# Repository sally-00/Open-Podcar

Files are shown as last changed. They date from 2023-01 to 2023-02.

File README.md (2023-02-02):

# Open Podcar 2.0

This is a project extended from [OpenPodcar](https://github.com/OpenPodcar/OpenPodcar).

We have changed components and improved the PCB layout to allow more flexibility in the system and ensure safty while operating the car.

At current stage, we have tested the linear actuator, almost finished the design of PCB except a few further improvements.
We will mount the linear actuator, manufactor the PCB and mount all the components in the close future.

## Linear Actuator Demostration
A demostration of controlling the linear actuator with the joystick which pass the steer command to the ESP32 through ROS using Wi-Fi is shown as follows.

<a href="https://youtu.be/pCknVWg_ioM
" target="_blank">Linear Actuator Joystick Control Demostration</a>

<a href="https://youtu.be/71_QIT539q4
" target="_blank">Linear Actuator Steering Demostration</a>

## PCB design
The final schematic of the PCB is shown as follows.

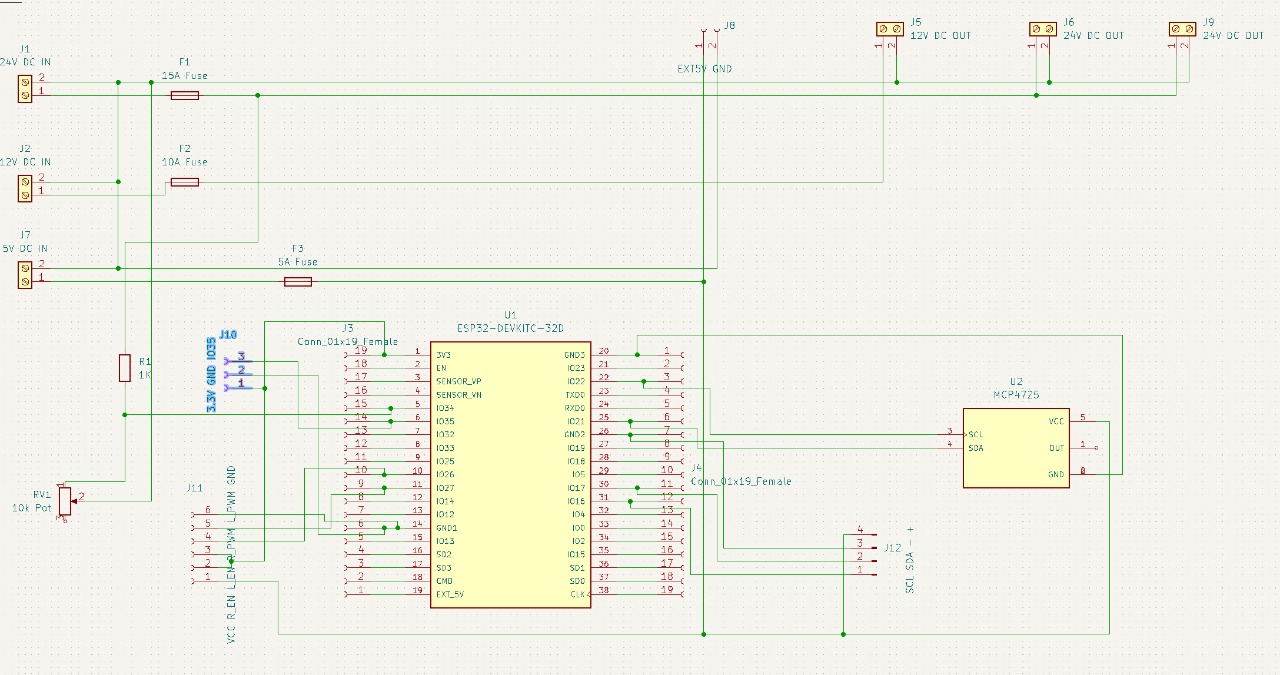
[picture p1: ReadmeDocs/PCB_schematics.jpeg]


The layout of the PCB at the current stage is shown as follows.

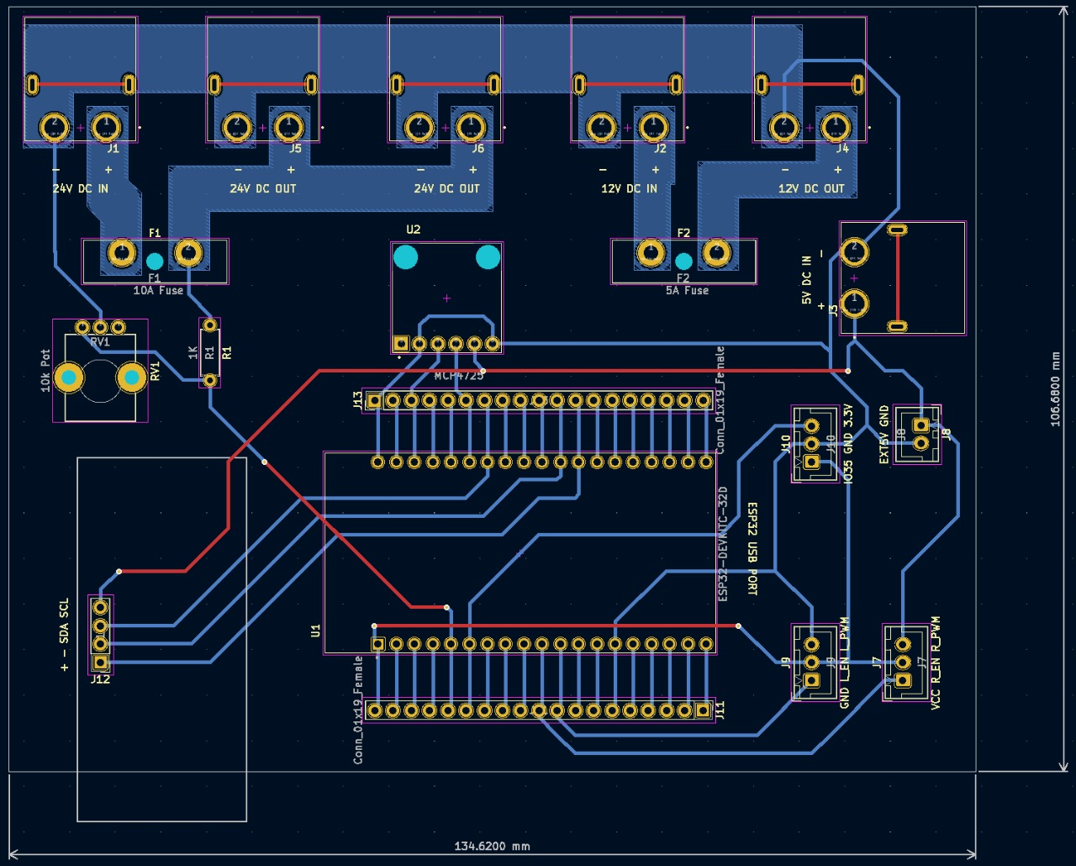
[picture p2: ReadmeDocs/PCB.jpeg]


## Bill of Materials

#### Vehicle
1 Gimson Robotics GLA750-P 12V DC linear actuator with position feedback (100mm stroke)

Metal bracket [linik to product](https://www.amazon.co.uk/dp/B08JV76967?ref_=cm_sw_r_apin_dp_HXTQEXMHK0DS5XG23BHY)

#### PCB

1 ESP32 [link to product](https://www.amazon.co.uk/XTVTX-Development-Wireless-Bluetooth-Frequency/dp/B09LCDJY8Z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)

1 DollaTek BTS7960 5.5V to 27V 43A High Power Motor Driver [link to product](https://www.amazon.co.uk/gp/product/B09H6MKWCJ/ref=ppx_yo_dt_b_asin_title_o00_s00?ie=UTF8&psc=1)

1 Digital to Analog Converter [link to product](https://www.digikey.co.uk/en/products/detail/sparkfun-electronics/BOB-12918/5140812?utm\_adgroup=Evaluation%20Boards%20-%20Digital%20to%20Analog%20Converters%20%28DACs%29&utm\_source=google&utm\_medium=cpc&utm\_campaign=Shopping\_Product\_Development%20Boards%2C%20Kits%2C%20Programmers&utm\_term=&productid=5140812&gclid=CjwKCAiAs8acBhA1EiwAgRFdw7jZpmNLCZSMikVMd7oKKiSc0wkz7JpF8sl4ogsQpp6ZFNUjAHO2KBoC\_PIQAvD_BwE)

1 Buck Converter Module 24V to 12V 15A [link to product](https://www.amazon.co.uk/dp/B01KQWWSLA/)

1 Buck Converter Module 12V to 5V 5A [link to product](https://www.amazon.co.uk/dp/B09NVZ6Y6J?ref_=cm\_sw\_r\_apin\_dp_F5CDBP8B0AESHGP8G7D0)

JST-XH connector [link to product](https://www.amazon.co.uk/YIXISI-460Pcs-Housing-Connector-Adapter/dp/B082ZLYRRN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)

Male XT60PW Gold Plated connector [link to product](https://www.switchelectronics.co.uk/male-xt60pw-gold-plated-connector-30a-amass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)

XT-60H connector [link to product](https://amzn.eu/d/4VwUmz3)

Fuse holder [link to product](https://uk.farnell.com/littelfuse/178-7017-0001/fuse-holder-pcb-r-a-blade/dp/310530?st=Ato%20fuse%20holder)

5A Fuse

10A Fuse

Potentiometer [link to product](https://uk.rs-online.com/web/p/potentiometers/8274990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)

Jumper wire [link to product](https://www.amazon.co.uk/VIPMOON-1-17mm-Multicolored-Flexible-Rainbow/dp/B07BLRNTXW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)

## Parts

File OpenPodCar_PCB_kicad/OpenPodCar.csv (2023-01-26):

Source: | C:\Users\skyks\Documents\KiCad\Projects\OpenPodCar - 2022\OpenPodCar\OpenPodCar.kicad_sch
Date: | 13/12/2022 15:54:15
Tool: | Eeschema (6.0.9)
Generator: | E:\Kicad\6.0\bin\scripting\plugins/bom_csv_grouped_by_value_with_fp.py
Component Count: | 18
Ref | Qnty | Value | Cmp name | Footprint | Description | Vendor
F1, | 1 | 15A Fuse | Fuse | Fuse:Fuseholder_Blade_ATO_Littelfuse_Pudenz_2_Pin | Fuse
F2, | 1 | 10A Fuse | Fuse | Fuse:Fuseholder_Blade_ATO_Littelfuse_Pudenz_2_Pin | Fuse
F3, | 1 | 5A Fuse | Fuse | Fuse:Fuseholder_Blade_ATO_Littelfuse_Pudenz_2_Pin | Fuse
J1, | 1 | 24V DC IN | Screw_Terminal_01x02 | TerminalBlock_MetzConnect:TerminalBlock_MetzConnect_Type011_RT05502HBWC_1x02_P5.00mm_Horizontal | Generic screw terminal, single row, 01x02, script generated (kicad-library-utils/schlib/autogen/connector/)
J2, | 1 | 12V DC IN | Screw_Terminal_01x02 |  | Generic screw terminal, single row, 01x02, script generated (kicad-library-utils/schlib/autogen/connector/)
J3, J4, | 2 | Conn_01x19_Female | Conn_01x19_Female | Connector_PinHeader_2.54mm:PinHeader_1x19_P2.54mm_Vertical | Generic connector, single row, 01x19, script generated (kicad-library-utils/schlib/autogen/connector/)
J5, | 1 | 12V DC OUT | Screw_Terminal_01x02 | TerminalBlock_MetzConnect:TerminalBlock_MetzConnect_Type011_RT05502HBWC_1x02_P5.00mm_Horizontal | Generic screw terminal, single row, 01x02, script generated (kicad-library-utils/schlib/autogen/connector/)
J6, J9, | 2 | 24V DC OUT | Screw_Terminal_01x02 | TerminalBlock_MetzConnect:TerminalBlock_MetzConnect_Type011_RT05502HBWC_1x02_P5.00mm_Horizontal | Generic screw terminal, single row, 01x02, script generated (kicad-library-utils/schlib/autogen/connector/)
J7, | 1 | 5V DC IN | Screw_Terminal_01x02 | TerminalBlock_MetzConnect:TerminalBlock_MetzConnect_Type011_RT05502HBWC_1x02_P5.00mm_Horizontal | Generic screw terminal, single row, 01x02, script generated (kicad-library-utils/schlib/autogen/connector/)
J8, | 1 | EXT5V GND | Conn_01x02_Female | Connector_PinHeader_2.54mm:PinHeader_1x02_P2.54mm_Vertical | Generic connector, single row, 01x02, script generated (kicad-library-utils/schlib/autogen/connector/)
J10, | 1 | 3.3V GND IO35 | Conn_01x03_Female | Connector_PinHeader_2.54mm:PinHeader_1x03_P2.54mm_Vertical | Generic connector, single row, 01x03, script generated (kicad-library-utils/schlib/autogen/connector/)
J11, | 1 | VCC R_EN L_EN R_PWM L_PWM | Conn_01x05_Female | Connector_PinHeader_2.54mm:PinHeader_1x05_P2.54mm_Vertical | Generic connector, single row, 01x05, script generated (kicad-library-utils/schlib/autogen/connector/)
R1, | 1 | 1K | R |  | Resistor
RV1, | 1 | 10k Pot | R_Potentiometer | Potentiometer_THT:Potentiometer_Bourns_PTV09A-1_Single_Vertical | Potentiometer
U1, | 1 | ESP32-DEVKITC-32D | ESP32-DEVKITC-32D | MODULE_ESP32-DEVKITC-32D
U2, | 1 | MCP4725 | ZC576300 | MODULE_ZC576300

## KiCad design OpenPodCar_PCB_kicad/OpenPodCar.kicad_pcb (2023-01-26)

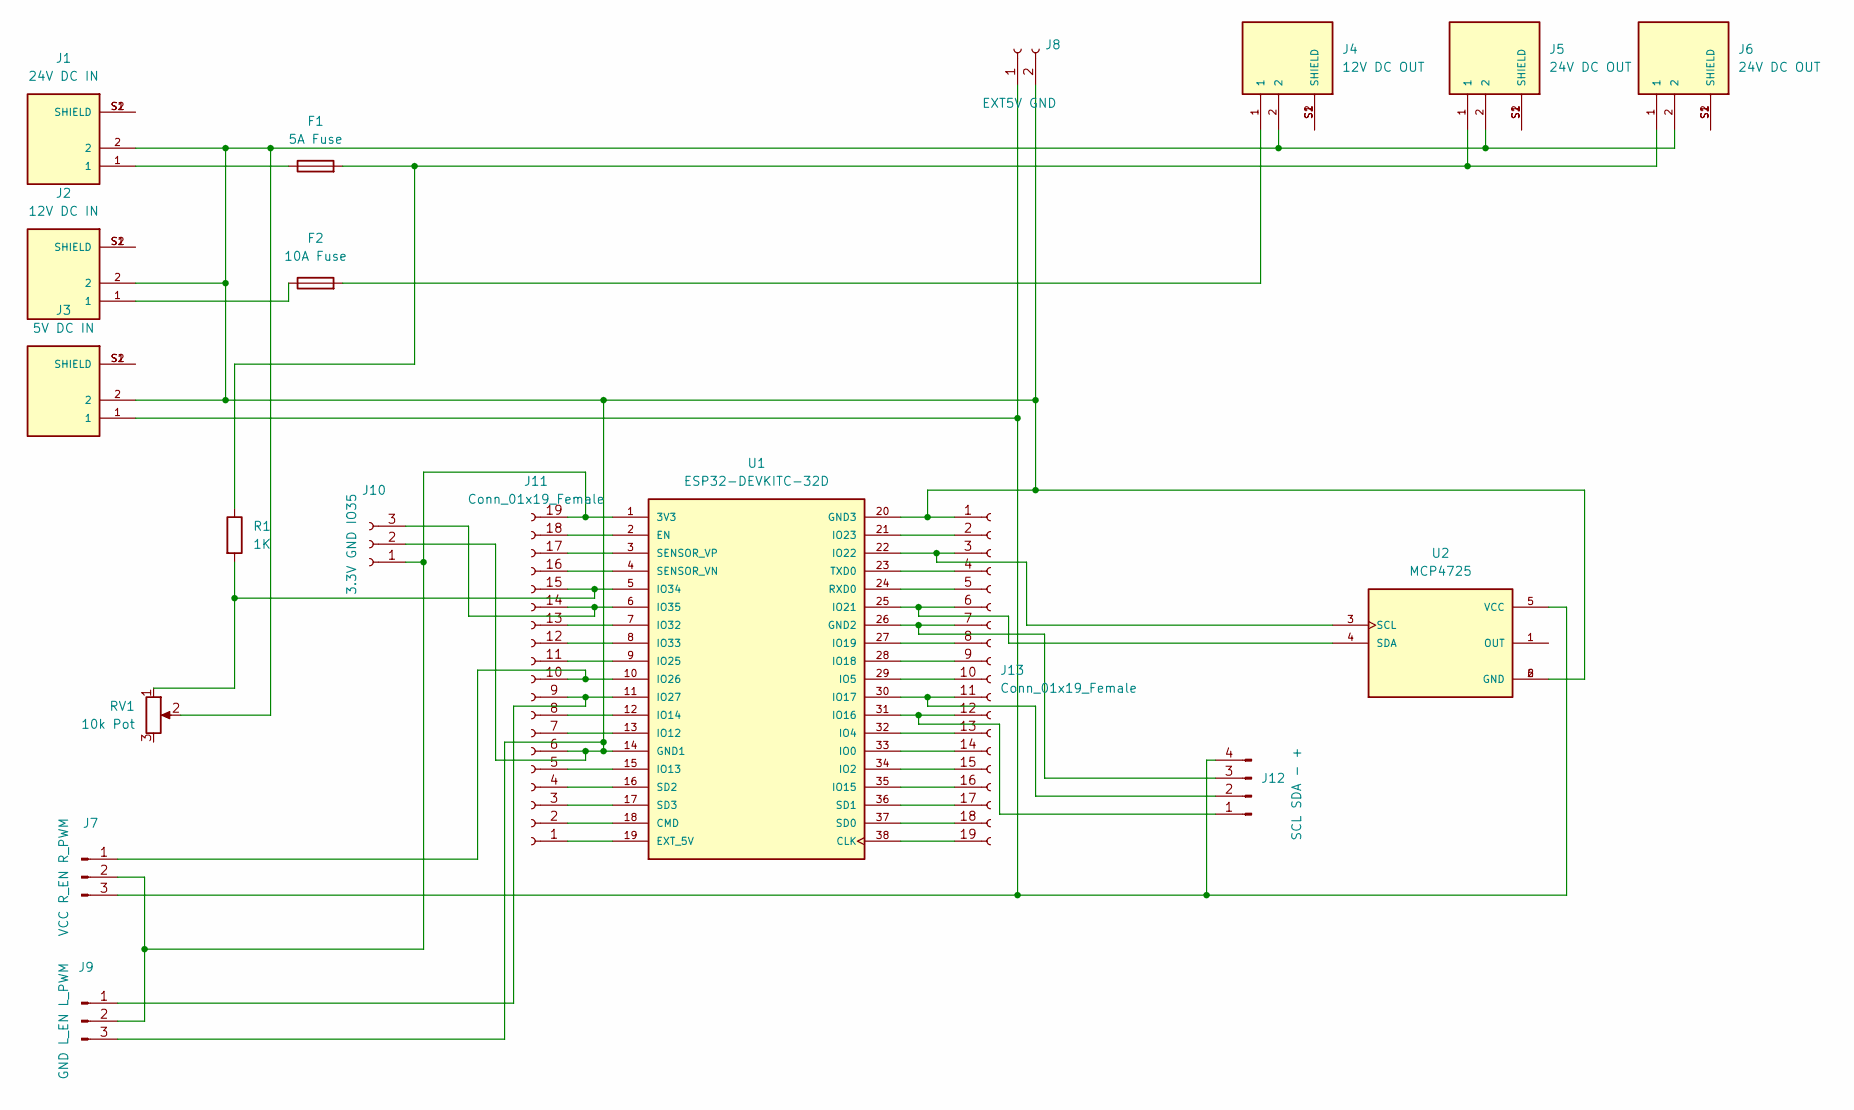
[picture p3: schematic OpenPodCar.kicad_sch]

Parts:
F1: 5A Fuse; Fuseholder_Blade_ATO_Littelfuse_Pudenz_2_Pin
F2: 10A Fuse; Fuseholder_Blade_ATO_Littelfuse_Pudenz_2_Pin
J1: 24V DC IN; AMASS_XT60PW-F; PARTREV V1.2
J2: 12V DC IN; AMASS_XT60PW-F; PARTREV V1.2
J3: 5V DC IN; AMASS_XT60PW-F; PARTREV V1.2
J4: 12V DC OUT; AMASS_XT60PW-F; PARTREV V1.2
J5, J6: 24V DC OUT; AMASS_XT60PW-F; PARTREV V1.2
J7: VCC R_EN R_PWM; JST_XH_B3B-XH-A_1x03_P2.50mm_Vertical
J8: EXT5V GND; JST_XH_B2B-XH-A_1x02_P2.50mm_Vertical
J9: GND L_EN L_PWM; JST_XH_B3B-XH-A_1x03_P2.50mm_Vertical
J10: 3.3V GND IO35; JST_XH_B3B-XH-A_1x03_P2.50mm_Vertical
J11, J13: Conn_01x19_Female; PinHeader_1x19_P2.54mm_Vertical
J12: SCL SDA - +; PinHeader_1x04_P2.54mm_Vertical
R1: 1K; R_Axial_DIN0207_L6.3mm_D2.5mm_P7.62mm_Horizontal
RV1: 10k Pot; Potentiometer_Bourns_PTV09A-1_Single_Vertical
U1: ESP32-DEVKITC-32D; MODULE_ESP32-DEVKITC-32D; PARTREV 4
U2: MCP4725; MODULE_ZC576300; PARTREV v14

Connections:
unnamed: F1.1, J1.1
unnamed: F1.2, J5.1, J6.1, R1.1
unnamed: F2.1, J2.1
unnamed: F2.2, J4.1
unnamed: J1.2, J2.2, J3.2, J4.2, J5.2, J6.2, J8.2, J9.3, J10.2, J11.6, J13.1, RV1.2, U1.14 (GND1), U1.20 (GND3), U2.2 (GND), U2.6 (GND)
unnamed: J1.S1 (SHIELD), J1.S2 (SHIELD)
unnamed: J2.S1 (SHIELD), J2.S2 (SHIELD)
unnamed: J3.S1 (SHIELD), J3.S2 (SHIELD)
unnamed: J4.S1 (SHIELD), J4.S2 (SHIELD)
unnamed: J5.S1 (SHIELD), J5.S2 (SHIELD)
unnamed: J6.S1 (SHIELD), J6.S2 (SHIELD)
unnamed: J7.2, J9.2, J10.1, J11.19, U1.1 (3V3)
unnamed: J10.3, J11.14, U1.6 (IO35)
unnamed: J11.1, U1.19 (EXT_5V)
unnamed: J11.2, U1.18 (CMD)
unnamed: J11.3, U1.17 (SD3)
unnamed: J11.4, U1.16 (SD2)
unnamed: J11.5, U1.15 (IO13)
unnamed: J11.7, U1.13 (IO12)
unnamed: J11.8, U1.12 (IO14)
unnamed: J9.1, J11.9, U1.11 (IO27)
unnamed: J7.1, J11.10, U1.10 (IO26)
unnamed: J11.11, U1.9 (IO25)
unnamed: J11.12, U1.8 (IO33)
unnamed: J11.13, U1.7 (IO32)
unnamed: J11.15, R1.2, RV1.1, U1.5 (IO34)
unnamed: J11.16, U1.4 (SENSOR_VN)
unnamed: J11.17, U1.3 (SENSOR_VP)
unnamed: J11.18, U1.2 (EN)
unnamed: J12.1, J13.12, U1.31 (IO16)
unnamed: J12.2, J13.11, U1.30 (IO17)
unnamed: J12.3, J13.7, U1.26 (GND2)
unnamed: J3.1, J7.3, J8.1, J12.4, U2.5 (VCC)
unnamed: J13.2, U1.21 (IO23)
unnamed: J13.3, U1.22 (IO22), U2.3 (SCL)
unnamed: J13.4, U1.23 (TXD0)
unnamed: J13.5, U1.24 (RXD0)
unnamed: J13.6, U1.25 (IO21), U2.4 (SDA)
unnamed: J13.8, U1.27 (IO19)
unnamed: J13.9, U1.28 (IO18)
unnamed: J13.10, U1.29 (IO5)
unnamed: J13.13, U1.32 (IO4)
unnamed: J13.14, U1.33 (IO0)
unnamed: J13.15, U1.34 (IO2)
unnamed: J13.16, U1.35 (IO15)
unnamed: J13.17, U1.36 (SD1)
unnamed: J13.18, U1.37 (SD0)
unnamed: J13.19, U1.38 (CLK)

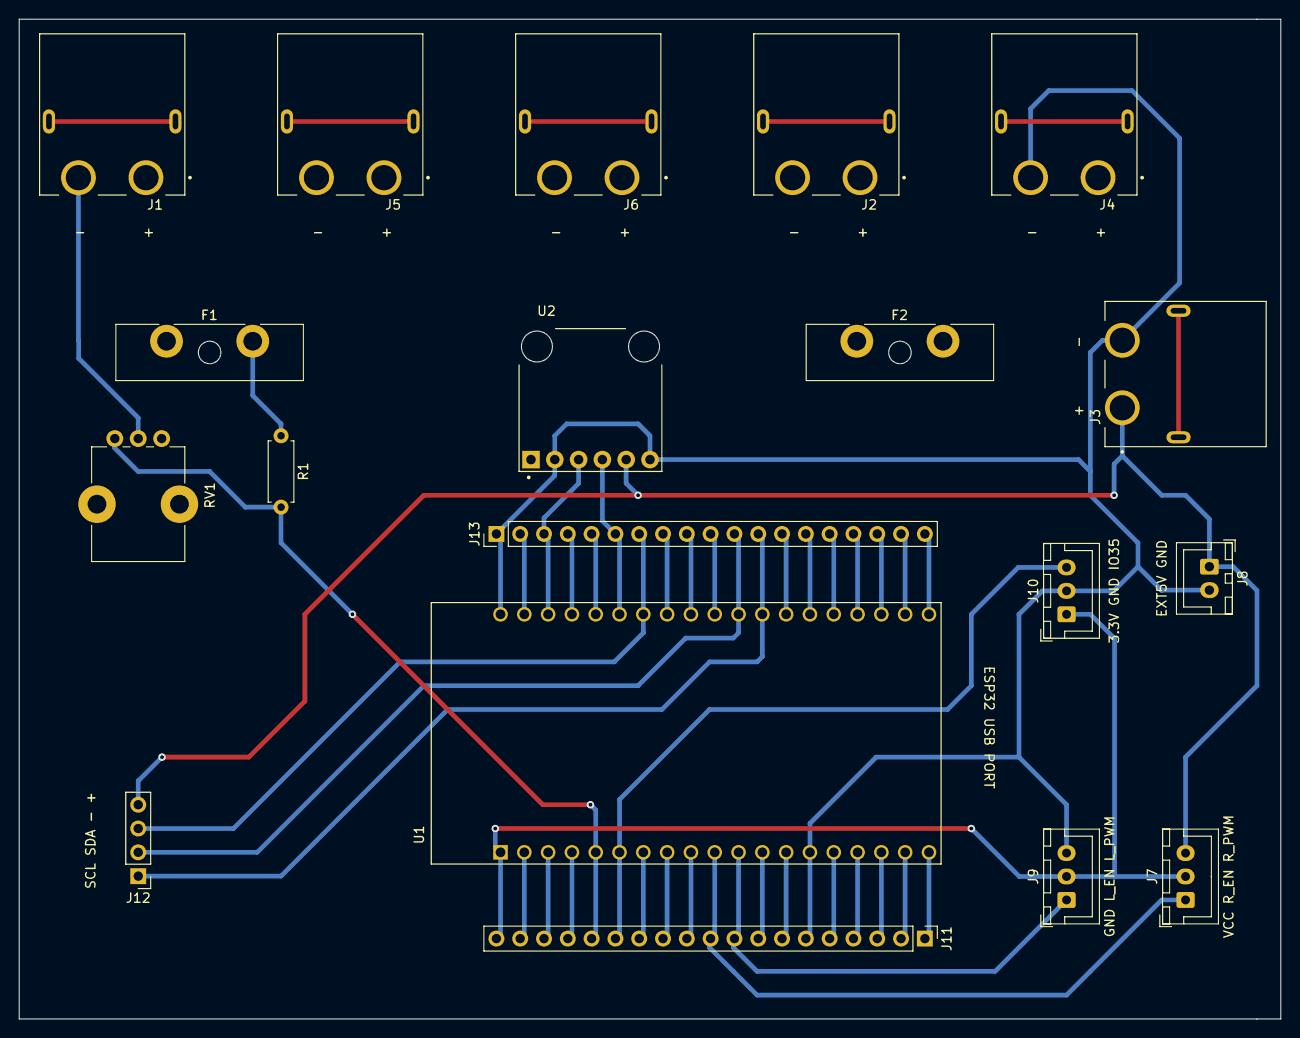
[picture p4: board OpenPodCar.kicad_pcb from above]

Board: 2 copper layers, 134.6 x 106.7 mm, 19 parts (0 on the bottom side), 48 nets.

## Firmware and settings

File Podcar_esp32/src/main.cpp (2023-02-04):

#include <iostream>
#include <Arduino.h>
#include <Wire.h>
#include <Adafruit_MCP4725.h>
#include <Adafruit_LEDBackpack.h>
#include <ros.h>
#include <chrono>
#include "motor.h"
#include "WiFiconection.h"
#include "utilities.h"
#include <std_msgs/String.h>
#include <std_msgs/Int16.h>
#include <std_msgs/Float32.h>

// variable ThrottleDACValue is used to drive the car, 
// make sure the values are correct for safety.
// Stopping the car is ThrottleDACValue = DACCentre, NOT 0.

using std::chrono::high_resolution_clock;
using std::chrono::duration_cast;
using std::chrono::duration;
using std::chrono::milliseconds;

/*
int Kp = 1, Ki = 1, Kd = 1;
unsigned long currentTime = 0, previousTime = 0, elapsedTime = 0;
int diff_sum = 0, diff_prev = 0;
float output;
*/

int direction, speed;
int current_pos, desired_pos, diff=0;
float desired_steer, desired_speed;
bool USE_ROS=false;

// setup DAC for speed control
Adafruit_MCP4725 Throttle;
uint16_t ThrottleDACValue = DACCentre; //Value for ThrottleDACValue after reset/powerup
float battery_voltage = 0;
uint16_t voltage_reading = 0;

// for display the battery voltage
Adafruit_7segment LCD = Adafruit_7segment();

// setup ros node with publish and subscrib
ros::NodeHandle nh;
// the range of speed and steer msg are both -1 to 1
void steering_msg_cb(const std_msgs::Float32 &msg){
    desired_steer = msg.data;
    if (desired_steer>=0 ){
        desired_pos = translate(desired_steer, 0, 1, LA_MIDDLE, LA_UPPER_LIMIT);
    }else{
        desired_pos = translate(desired_steer, -1, 0, LA_LOWER_LIMIT, LA_MIDDLE);
    }
}
void speed_msg_cb(const std_msgs::Float32 &msg){
    desired_speed = msg.data;
    // map desired_speed ([-1,1]) to ThrottleDACValue ([DAC_Lower_LIMIT, DAC_Upper_LIMIT])
    if (desired_speed >= 0){
        ThrottleDACValue = translate(desired_speed, 0, 1, DACCentre, DAC_Lower_LIMIT);
    }else{
        ThrottleDACValue = translate(desired_speed, -1, 0, DAC_Upper_LIMIT, DACCentre);
    }
    // ThrottleDACValue = msg.data;
}
ros::Subscriber<std_msgs::Float32> steer_sub("steering_cmd", &steering_msg_cb);
ros::Subscriber<std_msgs::Float32> speed_sub("speed_cmd", &speed_msg_cb);
std_msgs::Int16 int16_msg;
std_msgs::Float32 float32_msg;
ros::Publisher Linear_actuator_pos("linear_actuator_pos", &int16_msg);
ros::Publisher Battery_voltage("battery_voltage", &float32_msg);

// Forward declarations
void detect_I2C_device();
void reconnect_WiFi();
void read_steering(uint8_t iter);


void setup() {
    Serial.begin(115200);
    delay(100);
    
    if (USE_ROS){
        // connect to WiFi
        // if using iPhone, turn on Maximize compatibility
        // because by default, some only use 5GHz by bdefault
        // https://stackoverflow.com/questions/67084998/esp32-cant-connect-to-iphone-personal-hotspot
        WiFi.begin(SSID,PASS);
        Serial.print("WiFi connecting");
        while (WiFi.status() != WL_CONNECTED) {
            Serial.println("....");
            delay(100);
        }
        Serial.print(" connected! (");
        Serial.print(millis()*0.001);
        Serial.println("s");
        delay(100);
        
        // connect to ROS using WiFi, and register topics
        nh.getHardware()->setConnection(HOST_IP, serverPort);
        nh.initNode();
        Serial.println(" ros init complete ");
        nh.advertise(Linear_actuator_pos);
        nh.advertise(Battery_voltage);
        nh.subscribe(steer_sub);
        nh.subscribe(speed_sub);
        nh.spinOnce();
        delay(10);
    }

    // set up LCD
    Wire.begin();
    LCD.begin(0x70);

    // setup DAC
    Throttle.begin(0x62);
    delay(10);

    // setup Relay
    pinMode(Relay, OUTPUT);
    
    // setup PWM pins
    pinMode(RPWM_Output, OUTPUT);
    pinMode(LPWM_Output, OUTPUT);
    ledcSetup(Steering_CH_1, freq, resolution);
    ledcAttachPin(RPWM_Output, Steering_CH_1);
    ledcSetup(Steering_CH_2, freq, resolution);
    ledcAttachPin(LPWM_Output, Steering_CH_2);

    /* 
    // for checking the address of the I2C devices.
    while (true){
        detect_I2C_device();
    }
    */
    
    if (!USE_ROS){
        Serial.println("Please enter the desired position...");
        while (Serial.available()==0) {}
        desired_pos = Serial.parseInt();
    }else{
        desired_pos = LA_MIDDLE;
    }

    
}


void loop() {
    // set speed
    Throttle.setVoltage(ThrottleDACValue, false);

    // set relay
    digitalWrite(Relay, HIGH);

    // give command to the linear actuator
    if (abs(diff) < 15){
        brake();
    }else{
        if (diff > 0){ // linear actuator is too long
            speed = 255;
            direction = 0;
        }else{
            speed = 255; // linear actuator is too short
            direction = 1;
        }
        // become longer when direction=1, shorter when direction=0
        set_speed(speed, direction);
    }

    // For detecting I2C device detection
    //detect_I2C_device();

    if (USE_ROS){
        // reconnect to WiFi if connection is lost
        if(WiFi.status() != WL_CONNECTED){
            reconnect_WiFi();
        }
    }

    // getting the current steering (linear actuator position)
    // by averaging n times, and publish
    read_steering(1);

    // measure current battery voltage
    voltage_reading = analogRead(batt_vol);
    battery_voltage = voltage_reading * (3.3/1023) * RATIO;
    // print voltage on the LCD
    int v = round(battery_voltage * 100);
    boolean drawDots = false;
    LCD.writeDigitNum(0, (v / 1000), drawDots);
    LCD.writeDigitNum(1, (v / 100) % 10, drawDots);
    LCD.drawColon(true);
    LCD.writeDigitNum(3, (v / 10) % 10, drawDots);
    LCD.writeDigitNum(4, v % 10, drawDots);
    LCD.writeDisplay();
    if (USE_ROS){
        float32_msg.data = battery_voltage;
        Battery_voltage.publish( &float32_msg );
    }
    
    
    if (USE_ROS){
        // important to use spinOnce(process callbacks now). 
        // Had trouble connect to node if spinOnce is not used.
        // https://answers.ros.org/question/11887/significance-of-rosspinonce/
        nh.spinOnce();  
        delay(1); 
    }
    

    // don't need a PID because adding force does not move the actuator 
    /* with PID
    currentTime = millis();
    elapsedTime = currentTime - previousTime;
    diff_sum += diff;
    output = Kp*diff + Ki*diff_sum + Kd*(diff-diff_prev)/elapsedTime;
    previousTime = currentTime;
    diff_prev = diff;
    Serial.println(currentTime);
    Serial.println(previousTime);
    Serial.println(diff);
    Serial.println(output);
    */

}

void read_steering(uint8_t iter){
    auto t1 = high_resolution_clock::now();
    current_pos = 0;
    int count_num = 0;
    while (true){
        current_pos += analogRead(position_pin);
        count_num += 1;
        auto t2 = high_resolution_clock::now();
        /* Getting number of milliseconds as an integer. */
        auto ms_int = duration_cast<milliseconds>(t2 - t1);
        if (ms_int.count() > 50){
            break;
        }
    }
    current_pos = current_pos/count_num;
    // desired_steer:[-1,1] need to be mapped to desired_pos:[?]
    diff = current_pos - desired_pos;
    Serial.print("ThrottleDACValue: ");
    Serial.print(ThrottleDACValue);
    Serial.print(" ");
    Serial.print("desired_pos: ");
    Serial.print(desired_pos);
    Serial.print(" ");
    Serial.print("current_pos: ");
    Serial.print(current_pos);
    Serial.print(" ");
    Serial.print("num of readings: ");
    Serial.println(count_num);

    if (USE_ROS){
        int16_msg.data = current_pos;
        Linear_actuator_pos.publish( &int16_msg );
    }
}

void detect_I2C_device(){
    byte error, address;
    int nDevices;
    Serial.println("Scanning...");
    nDevices = 0;
    for(address = 1; address < 127; address++ ) {
        Wire.beginTransmission(address);
        error = Wire.endTransmission();
        if (error == 0) {
            Serial.print("I2C device found at address 0x");
            if (address<16) {
            Serial.print("0");
            }
            Serial.println(address,HEX);
            nDevices++;
        }
        else if (error==4) {
            Serial.print("Unknow error at address 0x");
            if (address<16) {
            Serial.print("0");
            }
            Serial.println(address,HEX);
        }    
    }
    if (nDevices == 0) {
        Serial.println("No I2C devices found\n");
    }
    else {
        Serial.println("done\n");
    }
    delay(5000); 
}

void reconnect_WiFi(){
    Serial.println("Reconnecting to WiFi...");
    WiFi.disconnect();
    WiFi.reconnect();
    Serial.print("WiFi reconnecting");
    while (WiFi.status() != WL_CONNECTED) {
        Serial.println("....");
        delay(100);
    }
    Serial.print("WiFi reconnected");
}

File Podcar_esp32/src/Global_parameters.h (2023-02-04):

/* ------------------------------------------------
 * 
 * [Pin out]
 *                  ● 3.3V                GND ●
 *                  ● Enable               23 ● 
 *                  ● 36(VP,i)             22 ●  SCL_PIN
 *                  ● 39(VN,i)          1(TX) ●x
 *                  ● 34(AD,i)          3(RX) ●x
 *      read analog ● 35(AD,i)             21 ●  SDA_PIN
 *                  ● 32(AD4)             GND ●
 *                  ● 33(AD5)              19 ● 
 *                  ● 25(AD18)             18 ● 
 *      RPWM_Output ● 26(AD19)              5 ● 
 *      LPWM_Output ● 27(AD17)             17 ● 
 *                  ● 14(AD16)             16 ● 
 *                x ● 12(AD15)        4(AD10) ● 
 *                  ● GND             0(AD11) ● x
 *                  ● 13(AD14)        2(AD12) ● x
 *                  ● 9(D2)          15(AD13) ● x
 *                  ● 10(D3)            8(D1) ● x
 *                x ● 11(CMD)           7(D0) ● x
 *                  ● 5V              31(CLK) ●
 *                         [USB]
 * -------------------------------------------------
 */
# include<stdint.h>


// motor driver
#define RPWM_Output 26
#define LPWM_Output 27
// channel for PWM
#define Steering_CH_1 0
#define Steering_CH_2 1
// for setting frequency an resolution
// https://docs.espressif.com/projects/esp-idf/en/latest/esp32/api-reference/peripherals/ledc.html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
// https://www.handsontec.com/dataspecs/module/BTS7960%20Motor%20Driver.pdf
#define freq 20000
#define resolution 8

// linear actuator position reading pin
#define position_pin 35

// This will change based on the resistor you use for the linear actuator and the linear actuator length
// range of gimson GLA750-P is [1~3680] -> [0 cm, 12.5 cm]
// the middle is 1300 -> 6.25 cm. map the steering based on the middle
uint16_t const LA_LOWER_LIMIT           = 0;
uint16_t const LA_UPPER_LIMIT           = 3680;
uint16_t const LA_MIDDLE                = 1300;

// setup limits for DAC; speed control
uint16_t const DACCentre                = 1679;  // new DAC value found in July 2019 -- Charles & Fanta 
uint16_t const DAC_Upper_LIMIT          = 2519; // DO NOT CHANGE - COULD DAMAGE SCOOTER CIRCUIT
uint16_t const DAC_Lower_LIMIT          = 1000; // DO NOT CHANGE - COULD DAMAGE SCOOTER CIRCUIT 
uint16_t const DACFullScale             = 4095; // 12bit DAC

// setup pins for reading battery voltage
#define batt_vol 34
#define RATIO  1/11

// I2C for DAC
#define SDA1 21
#define SCL1 22

// Relay pin
#define Relay 18

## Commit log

2023-01-22 added option for switching ROS off
2023-01-26 added PCB files
    [OpenPodCar.csv, OpenPodCar.kicad_pcb, OpenPodCar.kicad_sch]
2023-01-26 ESP32 linear actuator reading adjustment, ros msg receive adjustment
2023-01-26 publish battery voltage
2023-01-31 update PCB
2023-02-02 update README steer test
2023-02-04 Added voltage display
